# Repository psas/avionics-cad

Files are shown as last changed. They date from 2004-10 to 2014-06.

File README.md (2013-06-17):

# PSAS Schematics and Board Layouts

Main repo for all schematics and board designs on the rocket. This is
the main work of the [Avionics Team](http://psas.pdx.edu/avionics/).

To get started you'll need EAGLE CAD version 6.2 or greater.

## Directories:

 - `av3`: All files for the current rocket (2011 onwards)
 - `eagle`: CAM and script files and design rules for EAGLE CAD
 - `libraries`: Eagle libraries for differnt parts and projects
 - `lv1`: Historic boards and files for the [LV1 launch vehicle](http://psas.pdx.edu/Projects/#index2h3)
 - `lv2`: Historic boards and files for 2005 [launch of LV2.3](http://psas.pdx.edu/news/2005-08-20/)

## Naming Convention

    (rocketname)-(system-name)-[(sub-board-name)-][(sub-sub-board-name)-](version)

 - node1 = CAN Node v1, which was the PIC16F + SJA1000 design
 - node2 = CAN Node v2, which was the PIC18F + linear power supply (7805)
 - node3 = CAN Node v3, which was the PIC18F + SPS
 - node4 = USB Node v4, which is (LPC2148 ARM7 + SPSv2) 2006 capstone design
 - node5 = USB Node v5, which is (LPC2468 ARM7 + SPSv3) 2009 capstone design
 - node6 = Ethernet node v6, which is (STM32 Cortex-M4 + SPSv4) 2012 capstone design

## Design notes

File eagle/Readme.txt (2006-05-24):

PSAS EAGLE Schematics and Board Layouts

1. Naming Convention

 <rocketname>-<system-name>-[<sub-board-name>-][<sub-sub-board-name>-]<version>

 node1 = CAN Node v1, which was the PIC16F + SJA1000 design
 node2 = CAN Node v2, which was the PIC18F + linear power supply (7805)
 node3 = CAN Node v3, which was the PIC18F + SPS
 node4 = USB Node v4, which is (ARM7 + SPSv2) 2006 capstone design

2. Contents

 libraries              PSAS EAGLE Libraries (includes GPL-GPS parts)
 lv1-fc-1               LV1 flight computer (PIC17C74 + MAX197 + Presure + pyro)
 lv1-imu-1              LV1 inertial measurement unit (individual boards for each sensor)
 lv1-recovery-1         LV1 recovery/2m uplink board (PIC16F84 + DTMF decoder + Darlington pyro)
 lv1b-fc-1              LV1b flight computer (PIC17C766 + SRAM + connectors)
 lv1b-imu-1             LV1b inertial measurement unit (main board + Z axis daughter board)
 lv2-aps-1              LV2 avionics power supply
 lv2-imu-interface      LV2 inertial measurement unit node interface (uses lv1-imu-1)
 lv2-node2-connectors   LV2 node connectors
 lv2-node2-frontend     LV2 generic CAN node
 lv2-recovery           LV2 recovery/2m uplink board (PIC18F + interconnect to Tim's Rx)
 lv2-node4-frontend     LV2 generic USB node
 Readme.txt             This file
 scripts                Various useful EAGLE configurations and scripts

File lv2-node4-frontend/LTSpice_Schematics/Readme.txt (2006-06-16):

The schematic files (*.asc) only open with LTSpice/SwitcherCAD III which is available at

http://www.linear.com/company/software.jsp

When I opened up the file in PSpice for example it generated a text netlist.

There are no explicit notes about what various platforms it can run on but I used it on a Windows machine.

6/15/06

Jacob Davidson

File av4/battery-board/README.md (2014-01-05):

# AV4 Battery Board

This is a combined fuel gage, battery protection, cell balancing Smart Battery System PCB based on the BQ3060 "SBS 1.1-COMPLIANT GAS GAUGE and PROTECTION with CEDV".

# CAD and CAM

- All electronic CAD data is in the [eagle](eagle) directory.
- Design notes, Bill of Material (BOM), and functional requirements are in the [documentation](documentation) directory.
- All CAM data is in the TBD CAM directory.

# History

This board has *also* been a long time in the making. It was originally envisioned by Andrew back in 2009, started but placed on hold, and then all but finished by Bob in 2013. With the completion of the RocketNet Hub, this became the next most important project was thus picked back up by Kenny and Andrew Fall 2013. Michael finally finished it off in December 2013, and it was sent to production in Jan 2014.

# For more information

Please see <http://psas.pdx.edu/avionics>.

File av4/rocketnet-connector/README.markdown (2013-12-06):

# Rocketnet Connector

This is the standard connector we're going to use for cables between boards on
the rocket. It's built around small board-to-board connectors with a 3D printed
shroud and #2 hardware.

## Sizing Diagram

There are 3 different versions with a different number of pins

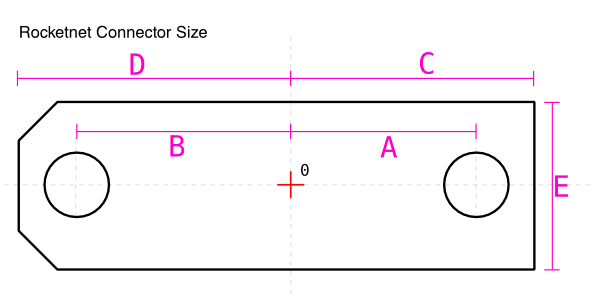
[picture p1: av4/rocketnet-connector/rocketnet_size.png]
Size diagram


**Dimentions for each version:**

 DIM |  14  |  16  |   18 
:---:| ----:| ----:| ------:
  A  |  6.9 |  7.5 |  8.135
  B  |  7.6 |  8.1 |  8.735
  C  |  8.6 |  9.1 |  9.7  
  D  |  9.2 |  9.7 | 10.3  
 C+D | 17.8 | 18.8 | 20     
  E  |  6.6 |  6.6 | 6.6

## Bolt Length

\#2 bolts: 14.5 mm

## Standoffs

Tap drill, \#50

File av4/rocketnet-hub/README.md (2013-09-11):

# Rocketnet Hub Overview

This board is the power and data distribution board for the AV3 avionics system. It has:

- Battery connector
   - Connect to the 4S1P Lithium-ion polymer battery pack
   - Also provides SMBus signals to talk with the TI BQ3060 fuel gauge IC on the battery pack.
- Umbilical connector
   - Provides shore power (usually 19V) from the umbilical cord
   - Ethernet, usually from the Launch Tower Computer (LTC)
   - Has the "rocketready" signal, a safety launch interlock.
- A TI BQ24725 battery charger IC, to charge the LiPo battery from shore power
- 7 "rocketnet" ports, which provide power and Ethernet to other rocketnet nodes (such as the Flight Computer (FC), IMU, etc).
- A Micrel KSZ8999 100Mbps Ethernet switch, which connects all of the rocketnet ports.
- An STM32F407 microcontroller that
   - Talks Ethernet to the KSZ8999 via MII
   - Switches and monitors power at each of the rocketnet ports.
   - Powers and manages the KSZ8999 Ethernet switch.

Here's a [block diagram](documentation/block_diagrams/blockdiagram.png).

# CAD and CAM

- All electronic CAD data is in the [eagle](eagle) directory
- Design notes, Bill of Material (BOM), and functional requirements are in the [documentation](documentation) directory.
- All CAM data is in the [mcu_page_combined_routed.cam](eagle/mcu_page_combined_routed.cam) directory.

# History

This board has been a long time in the making. It was originally envisioned by Andrew as replacement to the original USB LPC-based "Avionics Power System (APS)". It was then handed off to a 2012-2013 PSU ECE Capstone team, consisting of Jesse Hartley, Jackson Pugh, and Michael Woodruff. The board was checked and CAM'd by Andrew, built by [Sunstone Circuits](http://www.sunstone.com/), and then graciously assembled for free by [Screaming Circuits](http://screamingcircuits.com/). K, Theo, David, and Andrew brought the board up.

For full bring up information, including issues, fixes, modwires, and the like, see the [manufacturing and test log](documentation/mfg-and-test-log.md).

# For more information

Please see <http://psas.pdx.edu/avionics>.

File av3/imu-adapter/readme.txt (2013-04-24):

ADIS16405 IMU adapter boards

## "imu-adapter" - Adapt ADIS to node5 GFE

This board adapts the ADIS to the node5 (LPC2468 USB-based generic board). It was built, and worked.

## "imu-adapter-e407" - Adapt ADIS to Olimex STM32-E407 dev board

This board adapts the ADIS to the Olimex STM32-E407 (STM32F407 w/Ethernet) development board. It is a 1/16" single-sided PCB that must be mounted to the same mounting plane that the ADIS is mounted to. In the PCB, the holes for the ADIS and the ADIS connector are precisely spaced (see Analog Devices AN-1045 and ADIS datasheet for dimensions).

WARNING: Test points are on both sides of board, so if the board is against metal, make sure it's truly single-sided PCB.

## CAM Notes

When you run the 1 layer CAM job, you'll need to go in and edit the gerber files by hand in 'gerbv' in order to remove the ADIS mounting holes to the "right" of the actual adapter board.

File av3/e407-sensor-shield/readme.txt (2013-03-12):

This board is AV3's "sensor" sheild for an Olimex STM32-E407 development board. 

It connects the E407 board to:

- Analog Devices ADIS16405BMLZ 6DOF IMU with magnetometer (SPI)
- Invensense MPU-9150  6DOF IMU with magnetometer (I2C)
- Freescale MPL3115A2 pressure sensor (I2C)

It also brings up the Vin connection and the the ethernet jack pins in order to replace the 
coaxial jack and the ethernet jack with a RocketNet connector.

This daughter board requires the removal of the Ethernet, coaxial, and all "jumper" pin headers 
in order to fit.

TODO:

- Nothing yet!

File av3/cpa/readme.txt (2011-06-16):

Notes on v4 cylindrical patch antenna designs

2011/06/15 

Well, we've changed a few things! We've moved from the spreadsheet to a python script, and we've moved from 1.2 / 1.5 / 2.4 to 1.5 / 2.4 / 5.8 GHz. To make antennas, simply:

    run `./cpa-v4.py <frequency>`.
    Make sure there's a 'cam' directory.
    In EAGLE, open cpa-v4.cam and hit 'Process Job'.
    Use `gerbv` to sanity check the .gbx and .xln outputs.
    When you get the antennas back, see the 2004/07/03 instructions below to cut them out.

============================================================================================================================================================================

Notes on the v3 cylindrical patch antenna designs

2004/08/04

1.  Moved epsilon_r values to 2.20066 based on Tim's new calcs.

2.  Fixed 0.5Zin to 100 ohm 1/4 wave transformer on wifi antenna.

2004/08/03

1.  Added 0.010" on each side of the patch (near the seam) so we can sand off the edge to make it fit "perfectly".

2.  Moved screws that pierced the patch to the middle of the patch. Better electrically, didn't seem much worse mechanically.

3.  Removed the first 1/4wave transformer in the wifi antenna and replaced it with Zin feeds combining into a Zin/2 feed. The Zin/2 feed is then transformed to 100 ohms by a Zin/2 to 100 ohm 1/2 wave transformer, at which point it makes a 50 ohm line as usual.

4.  Added more space to the top and bottom of the PCB antenna so that the screw heads are at least 5h away from any radiator/microstrip.

5. Moved from the simplistic book-based patch length formula (with the 0.49 kludge factor) to the more elegant derived length model.

2004/07/30

1.  Cutting out the antennas:
    a. The patches should be cut out with the exacto blade splitting the 0.01" trace on the top and bottom of the board. This will require removing the 0.005" traces on either side, but there's not much to do about that (possible solution: we get the boards silk screened).
    b. The wide traces on the left and right are cut-out alignment traces; the excacto blade should go on the outside of the radiating patch and the inside of the alignment traces - thus when the board is cut out properly, the alignment traces won't be on the board.

2.  There are three elements stacked on top of each other at each screw location:
    a. The widest circle (located on on the tplace layer) is the outline of the counter-sunk #4 screw head.
    b. The middle circle (located on on the bplace layer) is the outline of the #4 screw hole drilled in the airframe.
    c. The smallest cicle, with the hour-glass symbol in it, is a 0.05" alignment hole drilled in the antenna PCB.
    
3.  The large circle located at the feedpoint (located on the bplace layer) is the outline of the 0.5" hole cut into the airframe in order to feed through the patch's SMA connector.

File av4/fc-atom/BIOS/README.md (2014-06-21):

The Atom board has an SPI EEPROM socket which holds 2MB of fun.  Everything the Atom needs for initial bootup lives here.  BIOS, its settings, and any other magic Intel goodness included.  We really just want the settings, but a different BIOS version would be confused by our settings binary segment.  So we may as well just grab the whole 2MB.  With a really slow interface like the BusPirate, this will cost you less than 10 minutes.

Kenny says to ask him questions about this process, if you have any.  There are all sorts of ways to drive SPI.  Here we use flashrom, which is probably packaged and available in your favorite Linux distro.  It supports many physical interface devices including the BusPirate.

Useful stuff:
+ http://flashrom.org/Bus_Pirate
+ https://www.sparkfun.com/products/9544
+ http://www.digikey.com/product-detail/en/5250/501-1311-ND/745102

An example run looks something like this:

```
$ time flashrom -p buspirate_spi:dev=/dev/ttyUSB0 -r SST25VF016B_dist.bin
flashrom v0.9.6.1-r1563 on Linux 3.11.0-20-generic (x86_64)
flashrom is free software, get the source code at http://www.flashrom.org

Calibrating delay loop... OK.
Found SST flash chip "SST25VF016B" (2048 kB, SPI) on buspirate_spi.
Reading flash... done.

real    8m9.453s
user    0m7.022s
sys     0m30.182s
```

If you want a dump of the active EEPROM contents directly from the Flight Computer, it could look like this:

```
root@psas:~# time flashrom -p internal -c SST25VF016B -r SST25VF016B_test.bin
flashrom v0.9.7-r1782 on Linux 3.14-1-amd64 (x86_64)
flashrom is free software, get the source code at http://www.flashrom.org

Calibrating delay loop... OK.
Found chipset "Intel ICH8M". Enabling flash write... OK.
Found SST flash chip "SST25VF016B" (2048 kB, SPI) at physical address 0xffe00000.
Reading flash... done.

real    0m2.268s
user    0m2.252s
sys     0m0.008s
```

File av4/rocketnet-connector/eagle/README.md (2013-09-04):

These files are PCBs for the rocketnet connector series. There are three different sizes:

14 pins = battery pack connector
16 pins = rocketnet connector
18 pins = umbilical connector

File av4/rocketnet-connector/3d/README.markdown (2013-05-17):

# Rocketnet But CAD Assembly

Files:

 - `rocketnet-connector-12pin.assemb.fcstd`: 12 pin version, full assembly
 - `rocketnet-connector-14pin.assemb.fcstd`: 14 pin version
 - `rocketnet-connector-16pin.assemb.fcstd`: 16 pin version

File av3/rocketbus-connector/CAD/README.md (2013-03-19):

# CAD Models for RocketBus Connector

Bare connectors tend to fall off rockets, so we have 3D printed plastic parts to accept bolts and lock down our cables.

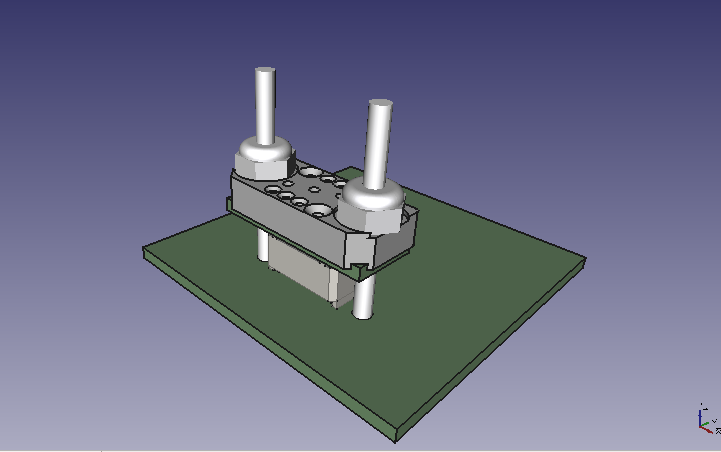
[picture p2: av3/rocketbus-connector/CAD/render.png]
Connector Render


## FreeCAD

Documents are made in [FreeCAD](http://free-cad.sourceforge.net/).

Files with `.part.` in the name are drawings of just a particular solid part.

`rockebus.assem.fcstd` is the full assembly with conncetors, bolts and boards all modeled. Printable parts can be exported by highlighting them and choosing File > export.

Version 0.2 printed at the [Electronics Prototyping Lab](http://psu-epl.github.com/) at PSU.

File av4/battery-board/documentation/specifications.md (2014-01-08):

# AV4 Battery Board Design Notes

## Overall Power System Design

At peak use, our avionics system is designed to handle about a (,30,50) W load. Our current best guess:

- FC = 15W
- RNH = 2W
- WiFi = 5W
- GPS = 1W
- IMU = 1W
- RC = 10W
- DV = 5W
- **Total** = 39 W

In terms of current, that's 2-3 A @ 16.7V or 3-5A @ 10V. That gives us a discharge current rating of (,3,5) A.

## Specifications

- MUST 
   - Measure pack voltage which can be (9,16.7,20) V.
   - Monitor pack current of (0.001,,5) A. 
   - Monitor charge ("coulomb counter") which can be (0, 4, 8) AHr with an accuracy of (,5,10)%.
   - Monitor battery pack temperature (-10,25,+80) deg C.
   - Be rated for (1,1.5,) C continuous charge and discharge currents (which would be (4,6,) A for an 4 AHr pack).
   - Provide electronic short circuit protection of 1.5 C (6 A for an 4 AHr pack), while not false-triggering on turn on capacitive transients of 100 uF.
   - Provide fused short circuit protection of (,2,5) C (which would be (,8,20) A for an 4 AHr pack), while not false-triggering on capacitive transients of 100 uF.
   - Fit on front of battery pack (,67 x 24,) mm.
   - Be shielded such that metal tools contact will not cause a short circuit in the battery.
   - Not have any components or leads that protrude into the battery compartment (excluding thermistors).
- SHOULD
   - Monitor the voltage on each cell.
   - Do cell balancing.
   - Handle deeply discharged batteries.
   - According to [[RocketNames]], the battery board components are all numbered in the 1xx regime.

## Tiered Overcurrent Protection

We have multiple tiers of overcurrent protection. In order of severity, we have:

- Local node OCP.
- TPS2450 circuit breaker chips on the RNH, custom set to a specific node at (0.5,,4) A.
- Battery board continuous overcurrent protection from the BQ3060 at 1.5C (,6,)A.
- 10 A fuse on the battery board; must handle 10-20A spikes but should blow if continuous.
- 20 A fuse on the battery breakout boards in each battery cell.

## Board layout notes

- Running board on OSH Park 4 layer process (5/5 design rules).
- We don't really need the 4 layers, but by doubling up on all four layers, we make 1 + 0.5 + 0.5 + 1 = 3 oz copper weight, which is perfect for high power.
- We're not pushing the design rules.

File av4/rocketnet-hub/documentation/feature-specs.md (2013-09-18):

# Features and Behaviors of the RocketNet Hub

TODO: This is just a rough draft.

## Modes

0. Boot mode
   - Check out saved state (armed/active).
1. Sleep mode (idle)
   - KSZ completely off.
   - All nodes are off.
   - Set interrupt on external GPIO (ACOK rising edge).
   - Go into deep sleep (all clocks off).
   - Goal: absolute minimum power consumpt (&lt; 5 mA)
   - Charge battery if shore power on (requires wakeup every 175 s to ping the BQ)
2. Debug mode (utility mode)
   - Ignores shore power on/off, otherwise just like active mode
   - Can not transition from debug to armed.
2. Active mode (startup/running mode)
   - KSZ is on.
   - One or more nodes are on.
   - Awake and looking for packets, acting on packets.
   - Monitoring battery voltage.
   - Charging battery when possible.
   - Can load power configurations (see below)
3. Armed mode (in flight)
   - Write armed state to file + last power configuration in case of restart
   - Everything on that should be on
      - Default configuration
      - Power configurations mapped to flight status?
   - Actively turning things back on that over current some number of times.
   - Resetting the KSZ and if no packets are getting through.
   - Resetting nodes (including the FC) if watchdog packets don't come through.
   - Broadcasting information on node power switches, current, voltage, etc.

## Mode Transitions

- Boot -> Armed
   - State saved file
- Boot -> Active
   - Shore power on
- Boot -> Sleep
   - Shore power off

- Sleep -> Active: 
   - Shorepower on (ACOK rising edge)

- Active -> Sleep:
   - Shore power: off
   - Nodes: all off || Vsys &lt; 12 V
   - Sleep command received

- Active -> Armed:
   - Arm command received (written to flash)

- Armed -> Active:
   - Disarm command received

- Active <-> Debug:
   - On debug start/stop command

- Debug -> Sleep:
   - Go to sleep
   
### Notes

- Send a "you're going to get shut down" packet some time before shutting off a node

## Command packets

- Turn on/off the KSZ
- Turn on/off any node
- Go to sleep
- Arm
- Disarm
- Transmit data packets
- Node-sepcific watchdog packets (each node sends it a ping, else the RNH power cycles it)

## Data packets

- Time
- Mode
- Shore Power Information
  - Shore power on/off
  - Shore power current (via IOUT)
- Battery charging info
  - Charging on/off
  - Battery charge current (via IOUT)
  - System voltage (shore power voltage when shore power on, battery voltage when shore power off)
- Power switches
   - KSZ power state
   - Node switch state, current from each node
- Future: BQ3060 battery state
   - Precise battery voltage, current, SOC, charge/discharge status, etc.
- Watchdog
   - Number of watchdog reboots
   - Time since last packet from each node

## Notes

- What's the current draw in each mode? How many hours can we last in each?
- We should send "arm" as a broadcast packet, and everyone could record the timestamp to sync their clocks.
- GPS could broadcast precise clock packets?
- Pre-broadcast-time packet could clear bus, then send time packet, to get real-time behavior.

## Quiescent current / "Shelf life"

Since:

- BQ24725 draws 20 uA when running directly from the battery without charging.
- The LTM8023 draws a couple of hundred microamps with no load.
- The STM32 in sleep mode draws hundreds of microamps.
- We have some current bleed through the link LEDs since they're running off the 3.3V supply (and why are they?).

Based on this, we should expect the quiescent draw of the whole RNH board of probably ~ 5 mA. Measured on bring up was ~ 3 mA. At 3 mA, that's about 1.5 months of life on a **fully charged** battery pack. On a fully depleted pack, this could kill the pack in a day or two. For this reason, we need to disconnect the battery when shore power is off and the avionics system is just sitting on the shelf.

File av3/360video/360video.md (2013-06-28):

Using H11F1 opto-isolator FET chip between APS "RC" output and GoPros "start" line. The FET grounds out the "start" line, and they all turn on and start recording.

We tested this system on the Agilent power supplies, and a forward curent I_f = 1 mA turned them on no problem.

The APS will run the H11F1 at 3.3V, Vf = 1.2 V so R = 2.1V/3mA = 700 ohms, so call it 750 ohms = 2.8 mA ish.

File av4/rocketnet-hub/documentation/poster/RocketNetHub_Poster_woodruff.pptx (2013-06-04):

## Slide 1

PSAS RocketNet Hub | Capstone 2012-2013

PSAS: Andrew Greenberg | Capstone Team : JJ Hartley, Jackson Pugh, and Michael Woodruff | Faculty Advisor: Dr. Richard Campbell

Overview
The capstone sponsor, Portland State Aerospace Society (PSAS), designs, builds, and launches high-power rockets. Their 2012-2013 Capstone project is a power management and communications solution for use in both their current and next generation launch vehicles. To accommodate the size and weight restrictions imposed by the physical characteristics of the current launch vehicle, the decision was made to pursue a highly integrated solution which would provide for all the power

Subsystem Design
Communications:
Initially specified as USB, the communications subsystem was changed to operate using the CAN Bus due to latency. This was then re-specified again to use 100Mbps Ethernet. A 10/100 Mbps 8+1 port switch-on-chip from Micrel was selected as it was the only device with the required functionality available to small-scale designers.
Microcontroller:
PSAS recently switched to STM32 microcontrollers for their nodes and requested that the same MCU be used to control this board. It is a compact ARM Cortex based microcontroller that is well suited to scalable embedded designs. The MCU’s primary functions are to control the battery charger, Ethernet switch, and each node’s power switch. Secondary functions are monitoring the battery’s charge state, current consumption of each node, and to reset the Ethernet switch if it enters a fault condition.
Power Domains:
The complexity of the this project was greatly increased by the requirement to accommodate five separate power domains on the board. There are two primary supplies, an 18VDC external supply and a four-cell battery pack. These feed the high voltage domain that powers the seven nodes and a 3.3V switching power supply. The 3.3V power domain supplies the onboard logic and a 2.1V LDO. The 2.1V power domain is used by the Ethernet switch.
Power Distribution:
Each of the seven nodes can be switched on or off by the MCU. By using a hot swap controller with integrated power FET, this solution allows for current ramping when a node is turned on, fault handling, and current monitoring all from a single 4mm x 4mm IC.
Battery charger:
The rocket’s battery is charged using an external 18VDC supply. This subsystem is built around a lithium polymer charger IC that monitors the battery during charging to prevent overheating and allows the current draw to be monitored while discharging.

Department of Electrical and Computer Engineering

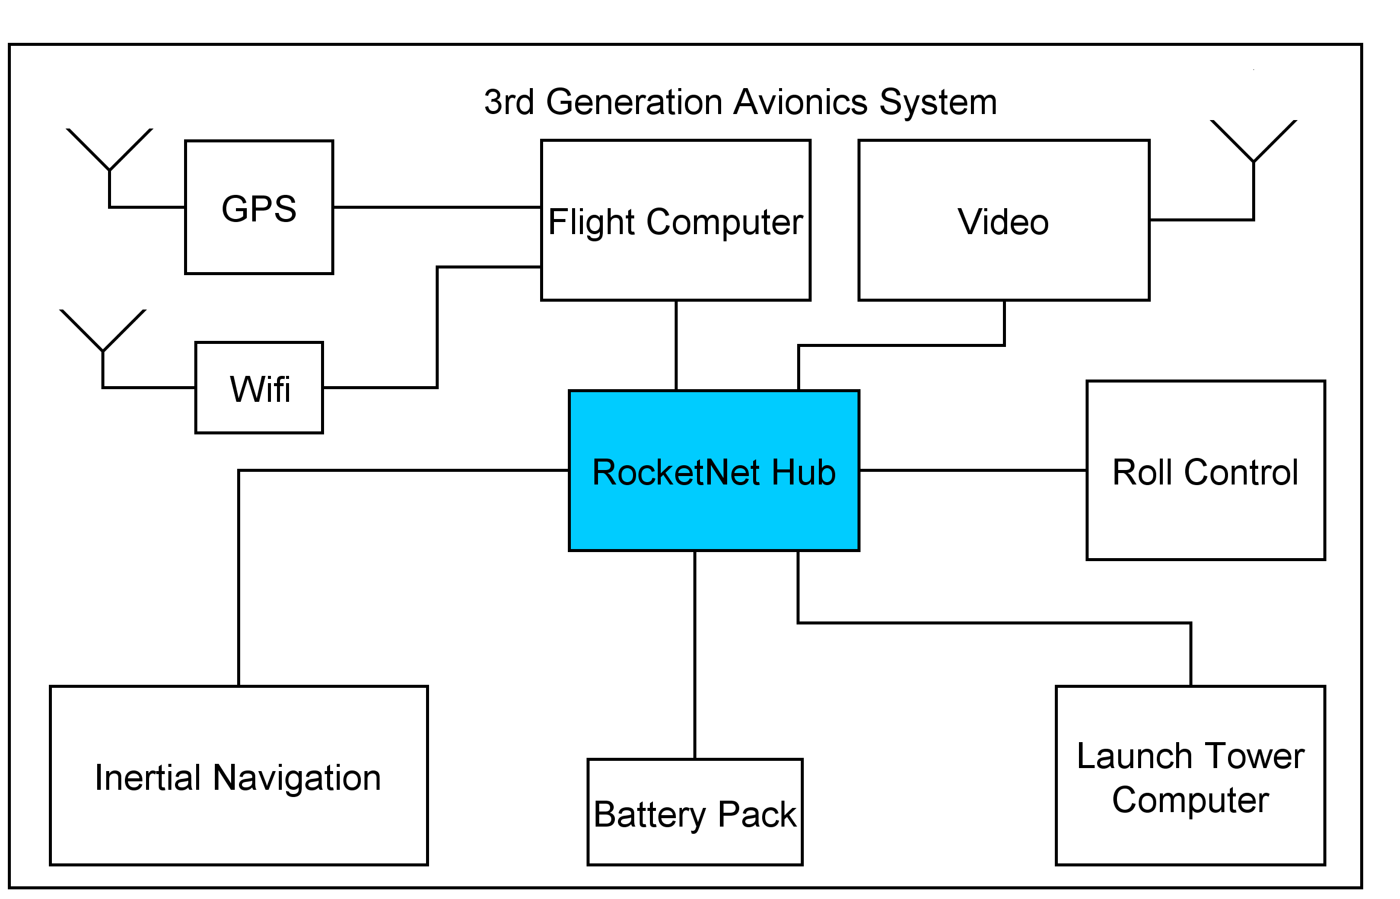
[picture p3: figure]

management functions as well as provide low
latency communication between all of the electronic
systems used in-flight on a single 6-layer PCB
with components placed on both sides.

Requirements
- Support seven nodes
- High reliability and fail-safe design
- Provide low latency inter-node communications
- Independent power management for each node in-flight and battery management pre-flight
- High efficiency switching power regulation from high voltage battery pack for low voltage logic
- Low-power consumption when in standby mode
- Charge the four-cell battery in under two hours

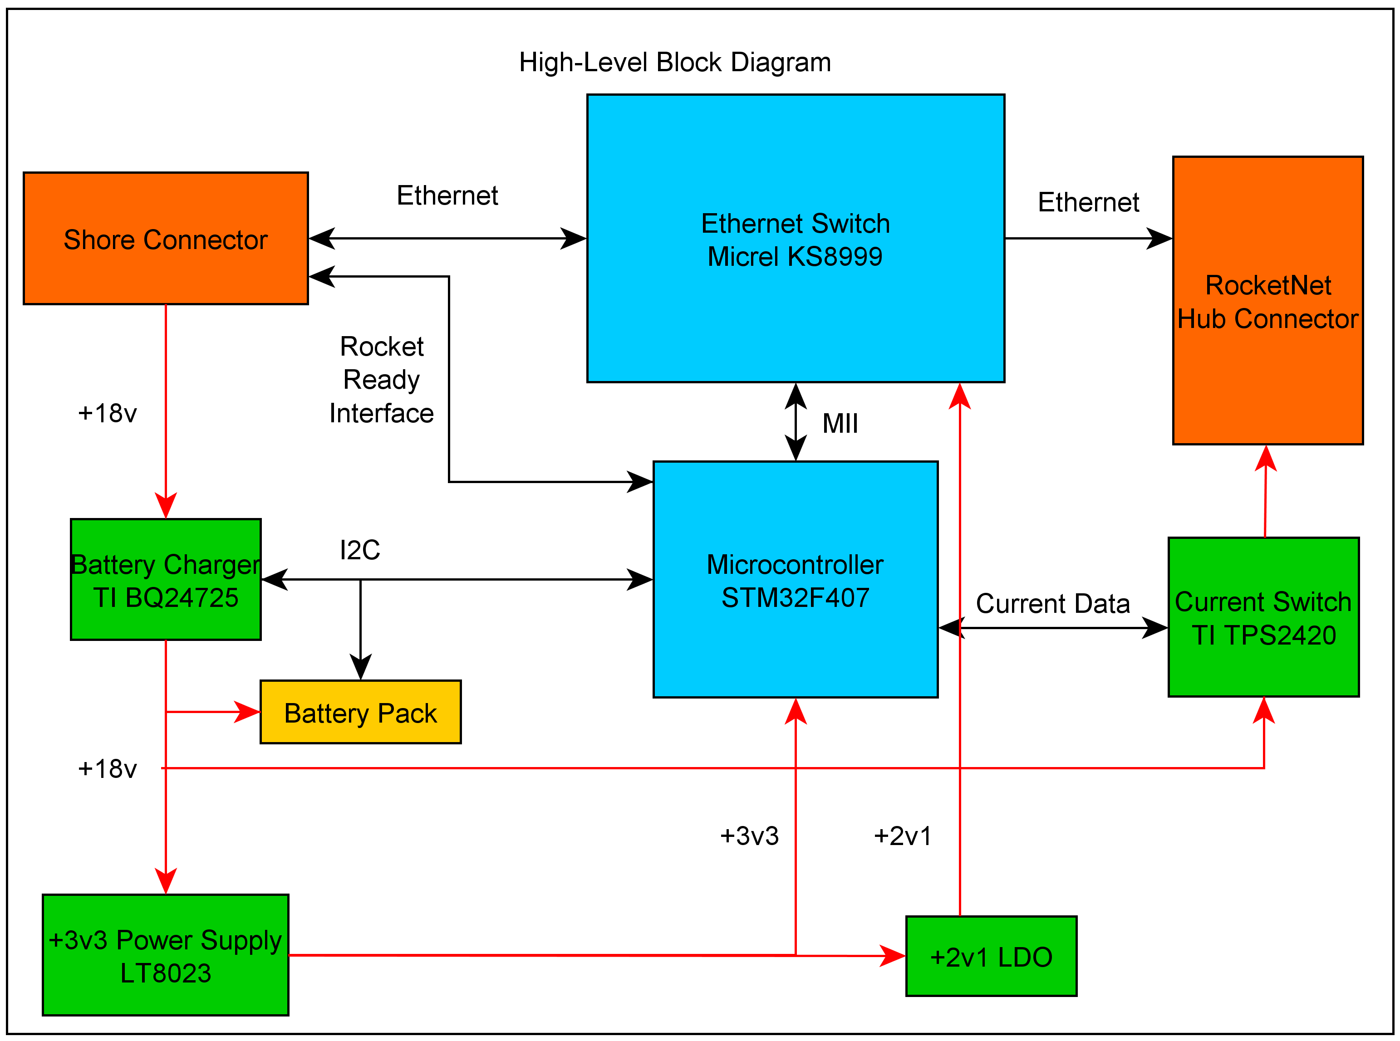
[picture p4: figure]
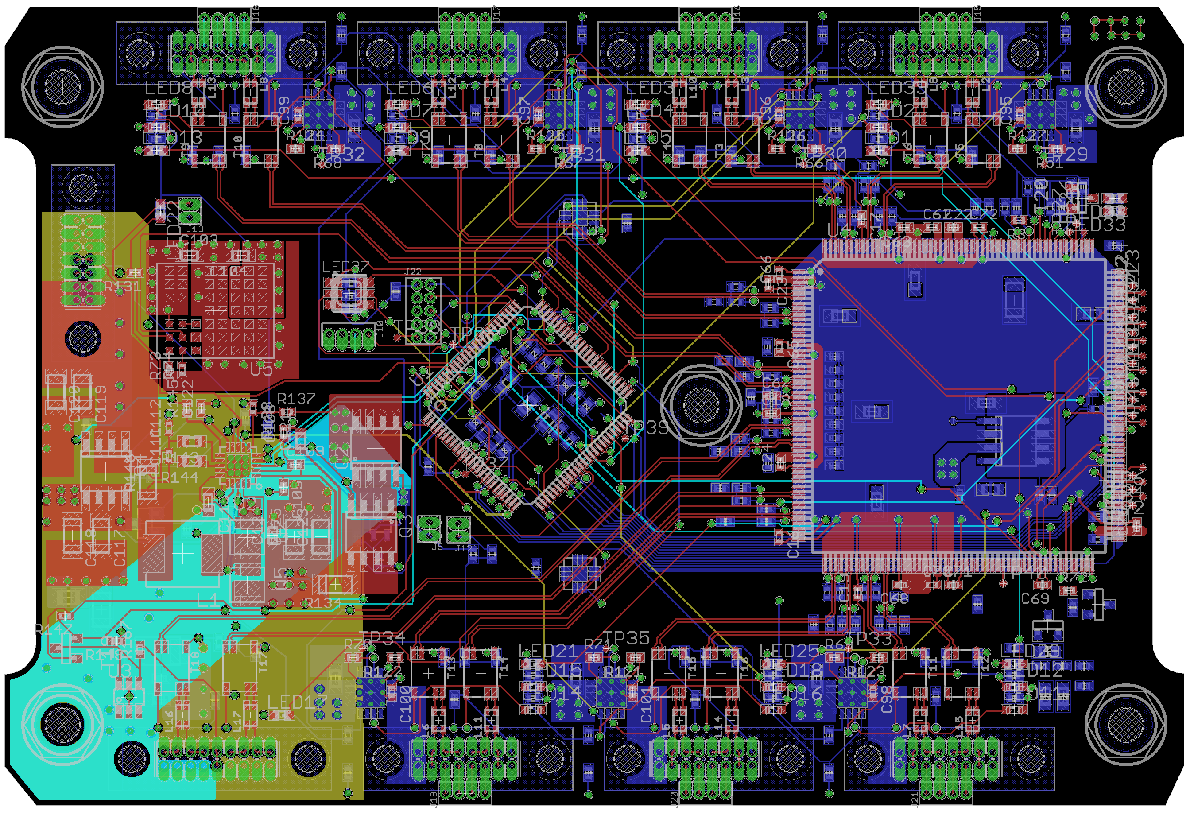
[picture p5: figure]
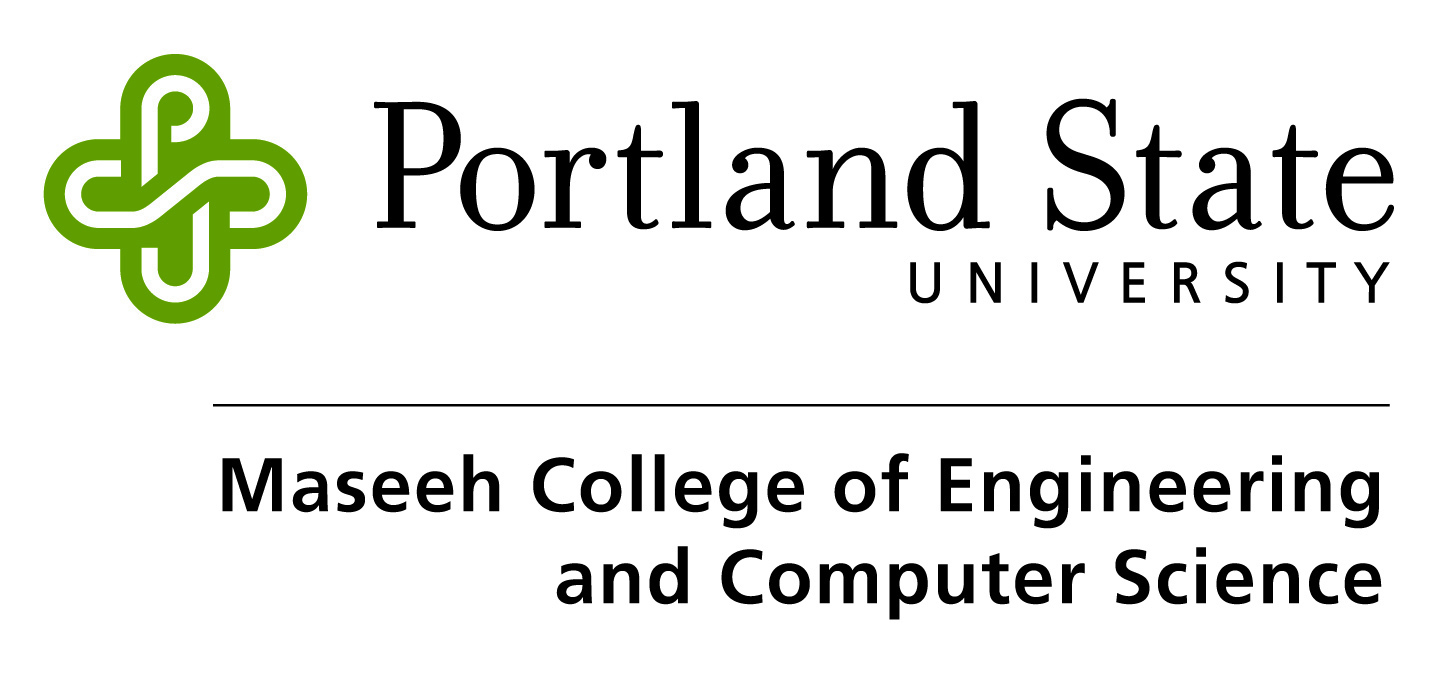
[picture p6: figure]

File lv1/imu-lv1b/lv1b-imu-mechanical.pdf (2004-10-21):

## LV1b imu-analog

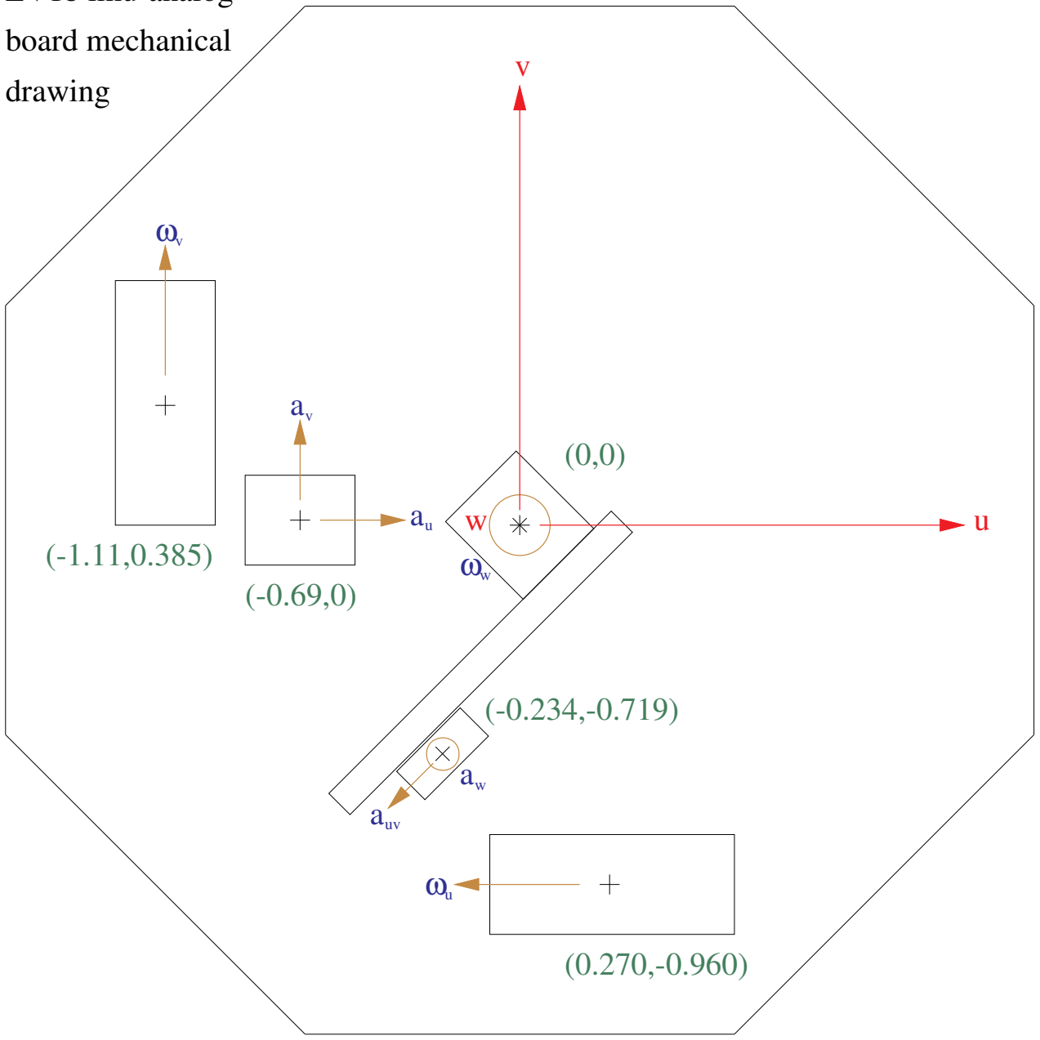
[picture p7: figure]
auv; board mechanical; drawing

accelerometer arrows indicate the sensitive axis in the direction of positive output

circles indicate the sensitive axis is up out of the plane of the drawing

gyro arrows indicate the sensitive axis, positive output follows the right hand rule

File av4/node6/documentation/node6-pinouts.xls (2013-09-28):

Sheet: Pins
Used: |  | 48
Free: |  | 52
PIN |  | FUNC1 | FUNC2 | FUNC3 | FUNC4 | FUNC5 | Notes
PA | 0 | UART4_TX | TIMER | WAKEUP
PA | 1 | ETH_RMII_REF_CLK | UART4_RX | TIMER |  |  | Ethernet PHY
PA | 2 | ETH_MDIO | USART2_TX | TIMER |  |  | Ethernet PHY
PA | 3 | USART2_RX | TIMER
PA | 4 | SPI1_NSS | SPI3_NSS
PA | 5 | SPI1_SCK | TIMER
PA | 6 | SPI1_MISO | TIMER
PA | 7 | ETH_RMII_CRS_DV | ETH_MII_RX_DV | SPI1_MOSI/ | TIMER |  | Ethernet PHY
PA | 8 | MCO1 | I2C3_SCL | TIMER |  |  | Ethernet PHY
PA | 9 | OTG_FS_VBUS | USART1_TX | I2C3_SMBA | TIMER |  | Debug connector
PA | 10 | OTG_FS_ID | USART1_RX/ | TIMER
PA | 11 | OTG_FS_DM | CAN1_RX | TIMER |  |  | Debug connector
PA | 12 | OTG_FS_DP | CAN1_TX | TIMER |  |  | Debug connector
PA | 13 | JTMS-SWDIO |  |  |  |  | JTAG connector
PA | 14 | TCK-SWCLK |  |  |  |  | JTAG connector
PA | 15 | JTDI | SPI3_NSS | SPI3_NSS | TIMER |  | JTAG connector
PB | 0 | TIMER
PB | 1 | TIMER
PB | 2 | BOOT1 |  |  |  |  | Tie low during startup and wakeup
PB | 3 | JTDO | SPI3_SCK | SPI1_SCK | TIMER |  | JTAG connector
PB | 4 | NJTRST | SPI3_MISO | SPI1_MISO | TIMER
PB | 5 | I2C1_SMBA | CAN2_RX | ETH_PPS_OUT | SPI1_MOSI | SPI3_MOSI
PB | 6 | I2C1_SCL | CAN2_TX | USART1_TX/ | TIMER |  | Debug connector
PB | 7 | I2C1_SDA | USART1_RX |  |  |  | Debug connector
PB | 8 | SPI2_NSS | I2C1_SDA | CAN1_TX
PB | 9 | SPI2_NSS | I2C1_SDA | CAN1_TX
PB | 10 | SPI2_SCK | USART3_TX
PB | 11 | ETH_RMII_TX_EN | I2C2_SDA | USART3_RX | TIMER |  | Ethernet PHY
PB | 12 | ETH_RMII_TXD0 | SPI2_NSS | I2C2_SMBA | CAN2_RX |  | Ethernet PHY
PB | 13 | ETH_RMII_TXD1 | SPI2_SCK | CAN2_TX | TIMER |  | Ethernet PHY
PB | 14 | SPI2_MISO | TIMER
PB | 15 | SPI2_MOSI | TIMER
PC | 0 | -
PC | 1 | ETH_MDC |  |  |  |  | Ethernet PHY
PC | 2 | SPI2_MISO
PC | 3 | SPI2_MOSI
PC | 4 | ETH_RMII_RX_D0 |  |  |  |  | Ethernet PHY
PC | 5 | ETH_RMII_RX_D1 |  |  |  |  | Ethernet PHY
PC | 6 | USART6_TX | TIMER
PC | 7 | USART6_RX | TIMER
PC | 8 | SDIO_D0 | TIMER |  |  |  | MicroSD card
PC | 9 | SDIO_D1 | MCO2 | I2C3_SDA | TIMER |  | MicroSD card
PC | 10 | SDIO_D2 | SPI3_SCK | USART3_TX |  |  | MicroSD card
PC | 11 | SDIO_D3 | UART4_RX | SPI3_MISO | USART3_RX |  | MicroSD card
PC | 12 | SDIO_CK | UART5_TX | SPI3_MOSI |  |  | MicroSD card
PC | 13 | - |  |  |  |  | NOTE: Kept energized when on Vbat
PC | 14 | OSC32_IN |  |  |  |  | RTC 32KHz xtal
PC | 15 | OSC32_OUT |  |  |  |  | RTC 32KHz xtal
PD | 0 | CAN1_RX
PD | 1 | CAN1_TX
PD | 2 | SDIO_CMD | UART5_RX | TIMER |  |  | MicroSD card
PD | 3 | -
PD | 4 | -
PD | 5 | USART2_TX
PD | 6 | USART2_RX
PD | 7 | -
PD | 8 | USART3_TX
PD | 9 | USART3_RX
PD | 10 | -
PD | 11 | -
PD | 12 | TIMER
PD | 13 | TIMER
PD | 14 | TIMER
PD | 15 | TIMER
PE | 0 | TIMER
PE | 1 | -
PE | 2 | -
PE | 3 | -
PE | 4 | -
PE | 5 | TIMER
PE | 6 | TIMER
PE | 7 | TIMER
PE | 8 | TIMER
PE | 9 | TIMER
PE | 10 | TIMER
PE | 11 | TIMER
PE | 12 | TIMER
PE | 13 | TIMER
PE | 14 | TIMER
PE | 15 | TIMER
PH | 0 | OSC_IN |  |  |  |  | 25 MHz xtal
PH | 1 | OSC_OUT |  |  |  |  | 25 MHz xtal
BOOT0 |  | BOOT0 |  |  |  |  | Debug connector, but pull down on board.
NRST |  | !RESET |  |  |  |  | Debug connector
VBAT |  | PWR |  |  |  |  | To RTC backup supply: supercap or coin cell
PWR | 0 | PWR
PWR | 1 | PWR
PWR | 2 | PWR
PWR | 3 | PWR
PWR | 4 | PWR
PWR | 5 | PWR
PWR | 6 | PWR
PWR | 7 | PWR
PWR | 8 | PWR
PWR | 9 | PWR
PWR | 10 | PWR
PWR | 11 | PWR
PWR | 12 | PWR
PWR | 13 | PWR
PWR | 14 | PWR
PWR | 15 | PWR

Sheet: JTAG Connector
JTAG Connector

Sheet: Debug Connector
Pin | STM32 PIN |  | FUNC1 | Notes
1 | PA | 9 | OTG_FS_VBUS | USB /dev/ttyACM0
2 | PA | 11 | OTG_FS_DM | USB /dev/ttyACM0
3 | PA | 12 | OTG_FS_DP | USB /dev/ttyACM0
4 | PB | 6 | USART1_TX/ | Debug UART
5 | PB | 7 | USART1_RX | Debug UART
6 | BOOT0 |  | BOOT0 | Use UART bootloader
7 | NRST |  | !RESET | Reset
8 | Vcc |  | Vcc | 3.3V ("Vtarget")
9 | GND |  | GND | GND
10 | ? |  | ? | Misc - Either to breakout pin or GPIO

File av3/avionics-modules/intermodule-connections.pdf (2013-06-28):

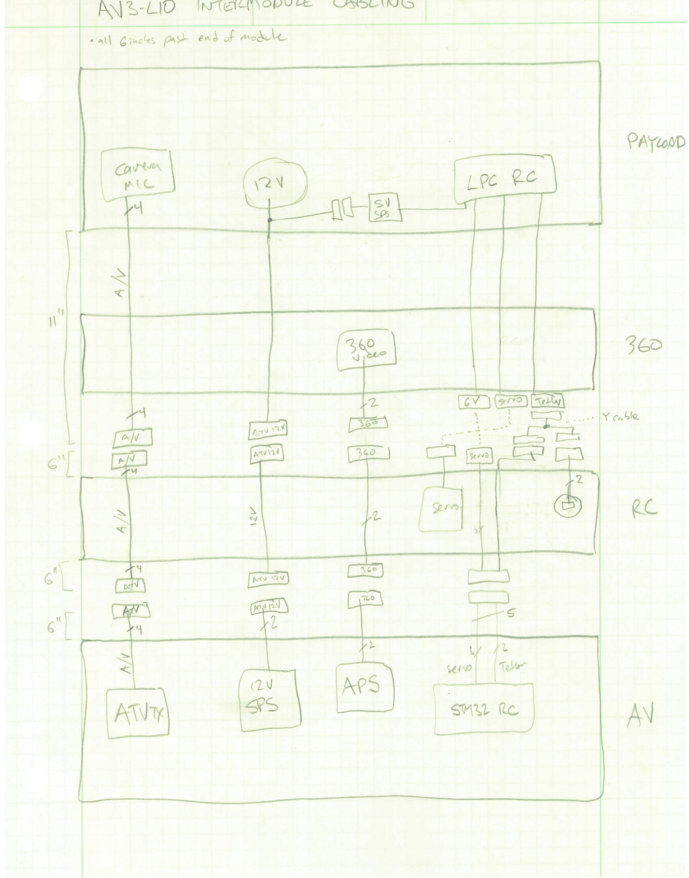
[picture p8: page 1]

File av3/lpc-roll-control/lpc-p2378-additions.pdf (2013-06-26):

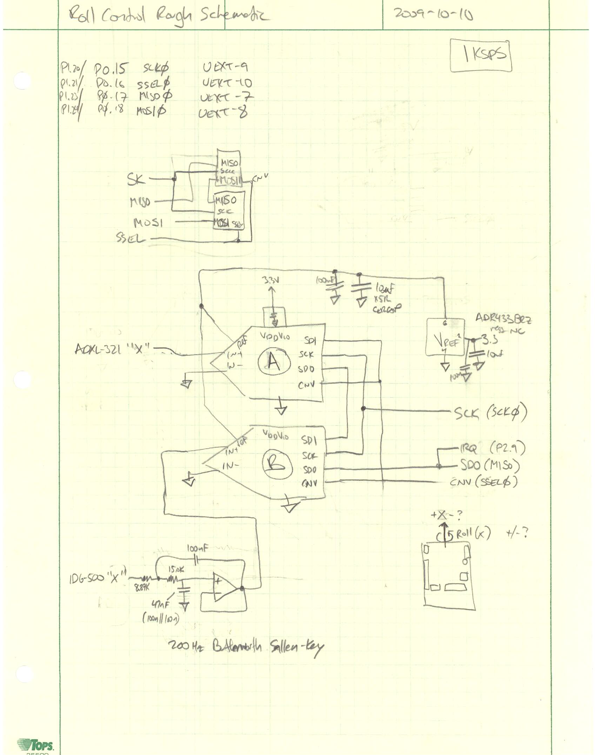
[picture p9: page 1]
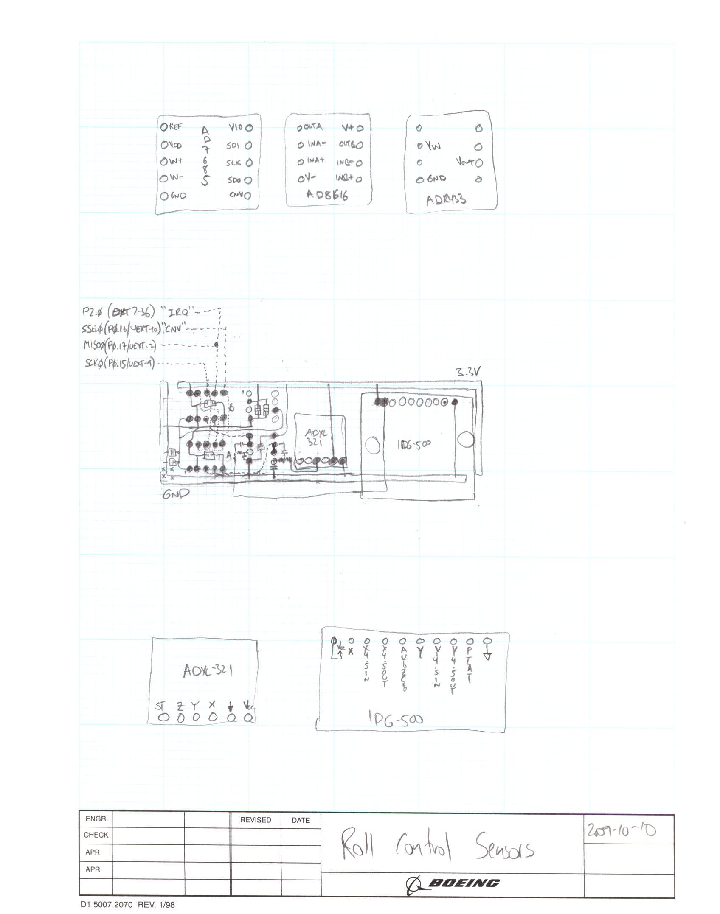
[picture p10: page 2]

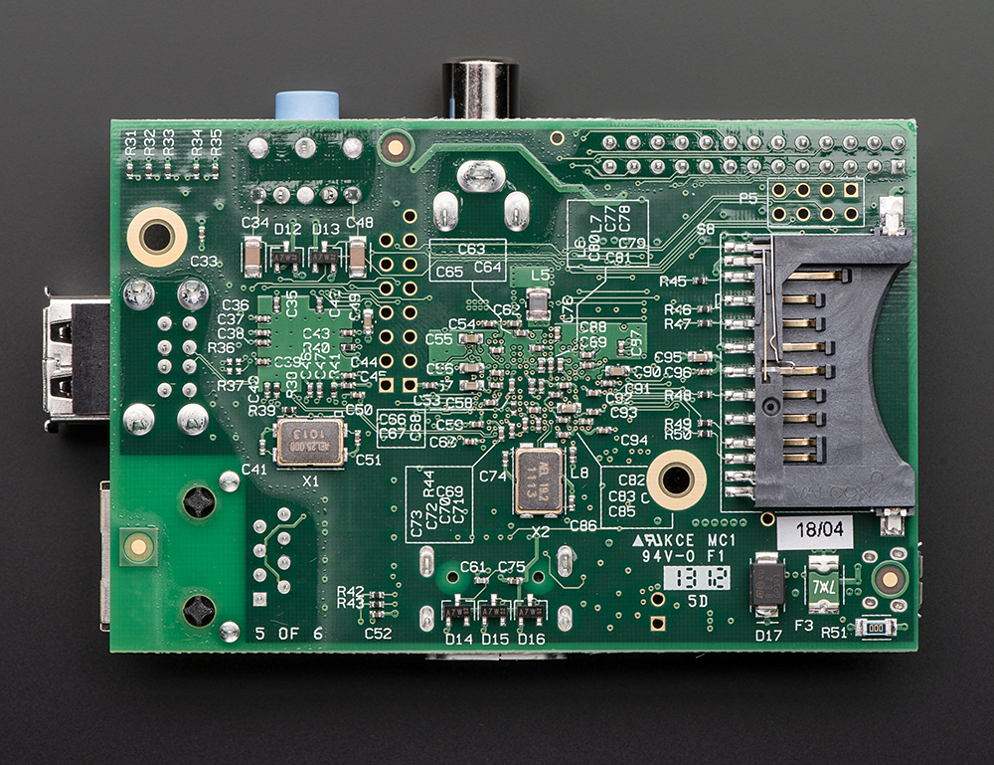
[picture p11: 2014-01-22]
av4/raspi-camera/datasheets/modelb_bottom.jpg

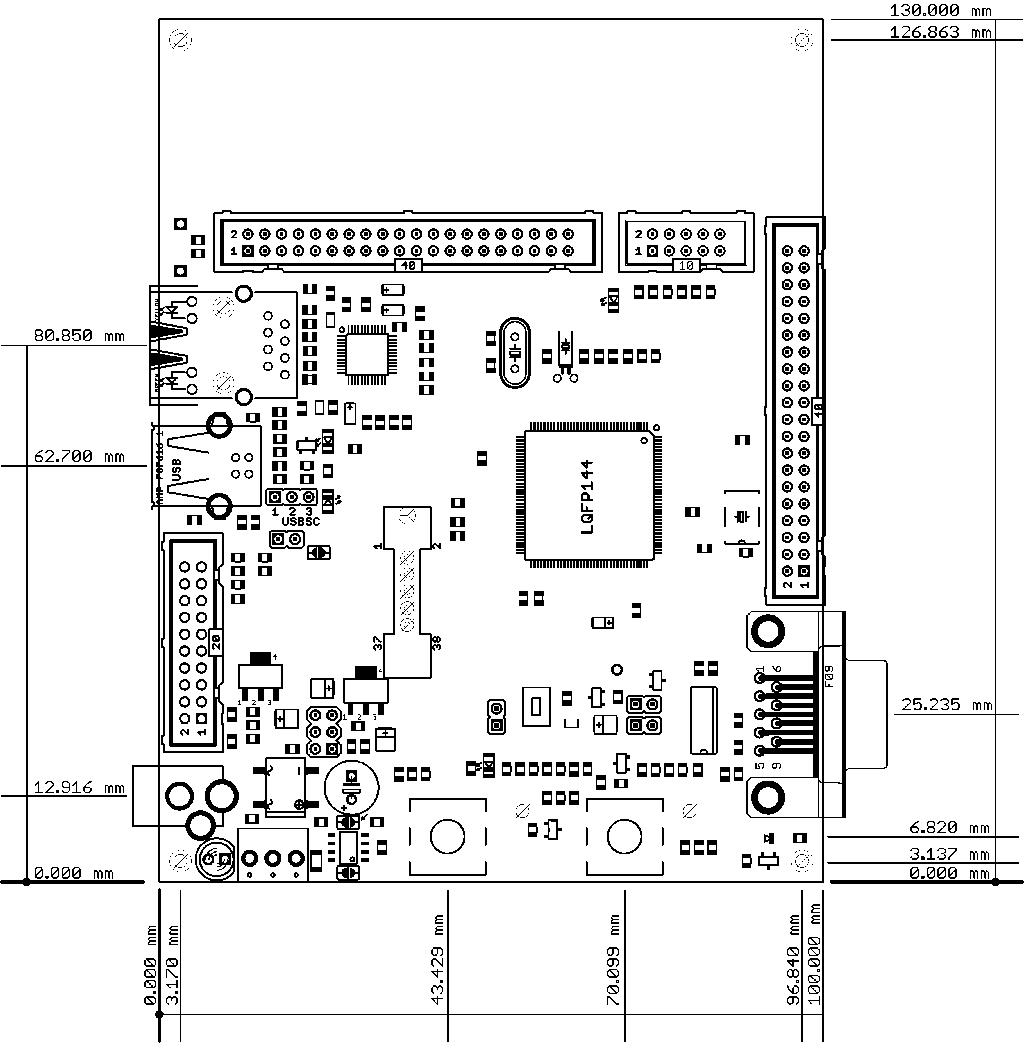
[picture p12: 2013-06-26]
av3/lpc-roll-control/LPC-P2378_Rev-B-dimensions.gif

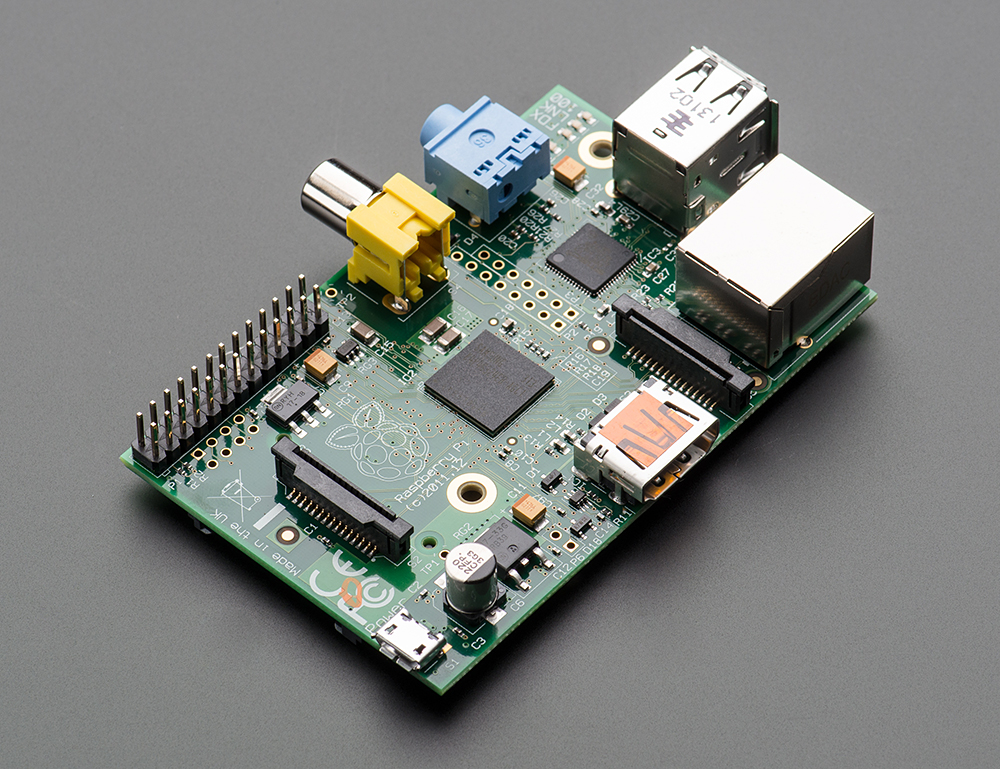
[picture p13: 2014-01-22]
av4/raspi-camera/datasheets/modelb_orthagonal.jpg

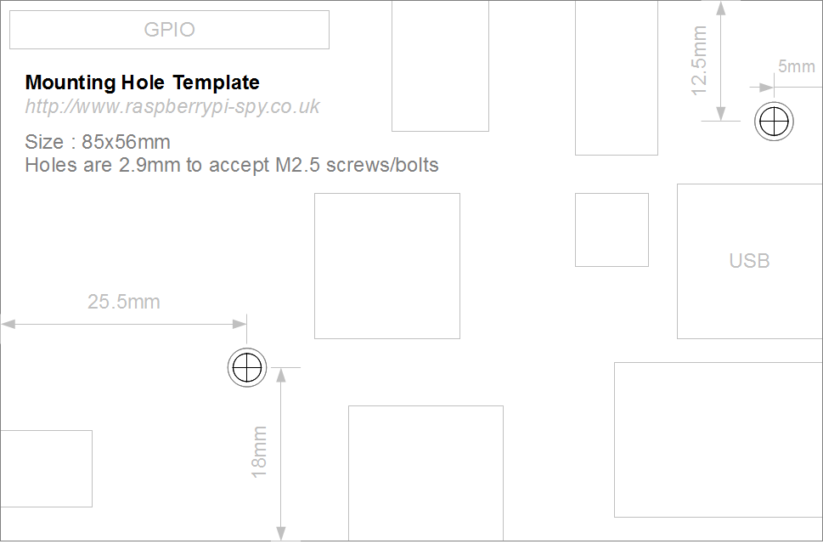
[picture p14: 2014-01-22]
av4/raspi-camera/datasheets/Raspberry-Pi-Mounting-Hole-Template.png

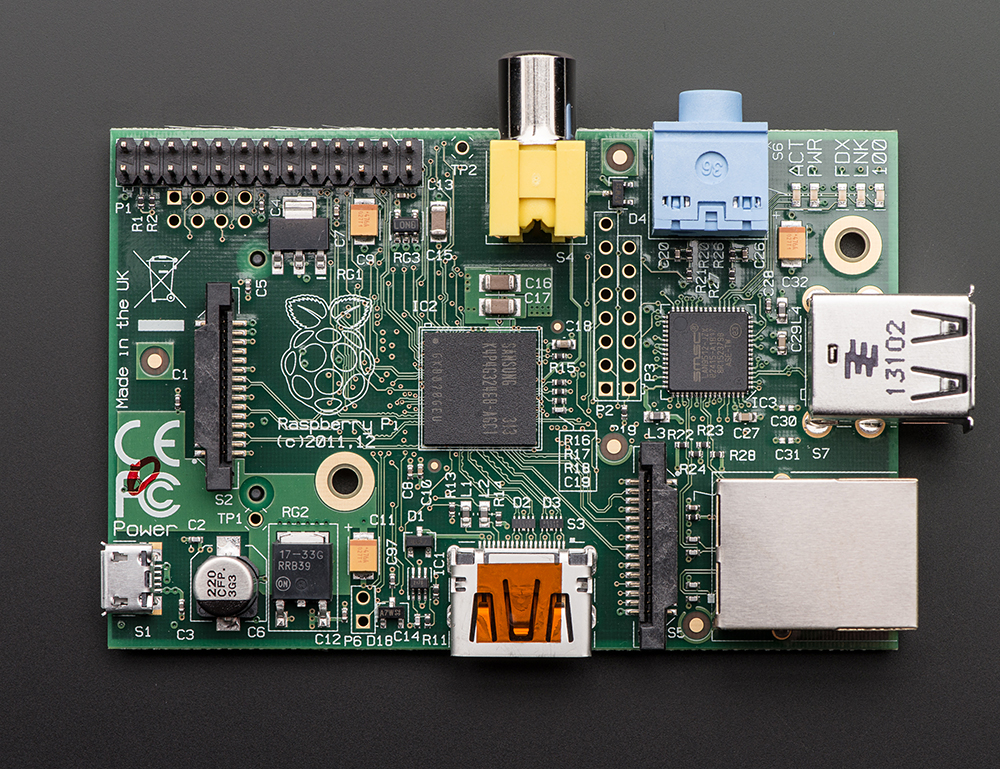
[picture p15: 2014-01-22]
av4/raspi-camera/datasheets/modelb_top.jpg

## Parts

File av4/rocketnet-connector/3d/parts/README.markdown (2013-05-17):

# Parts For CAD Assembly

**Manafacturer Parts**

STEP files from the manafacturer

 - `m50-3150642_asm.stp`: 12 Pin Female Connector
 - `m50-3150742_asm.stp`: 14 Pin Female Connector
 - `m50-3150842_asm.stp`: 16 Pin Female Connector
 - `m50-3500642_asm.stp`: 12 Pin Male Connector
 - `m50-3500742_asm.stp`: 14 Pin Male Connector
 - `m50-3500842_asm.stp`: 16 Pin Male Connector

**PSAS Parts**

Sub assembly

 - `Base_CircuitBoard.stp`: Plane circuit board base.
 - `Daughter_Board.part.fcstd`: FreeCad document of daughter board
 - `Daughter_Board.stp`: Step file export of daughter board
 - `no2_hex_screw.part.fcstd`: #2 Hex head screw freecad doc
 - `no2_hex_screw.stp`: #2 hex head screw part

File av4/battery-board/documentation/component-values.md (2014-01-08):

## Component Value Calculations

### F100 main fuse - 10A fast blow 1206 - LittleFuse 0501010.WR (DK F2919CT-ND)

**Purpose:** F100 is the main fuse that provides emergency overcurrent, over voltage (via D100), and reverse voltage (via D100) protection.

**Notes:** It's a 10A fuse in a 1206 package. 0.5679 Ohm resistance rated for 32V. F100 should take 10A forever, 30A @ 10s, 35A @ 1s, 42A @ 100ms, 52A @ 10ms, and and about 100A @ 1ms. During normal conditions, we expect to not pull more than 5A out of the battery pack, either in or out, ever, for more than a few hundred ms. We might get that much during a short condition from a node, but shorts in nodes should be handled by the TPS chips on the RNH. For extreme circumstances, each LiPo cell has an internal 20 A fuse (of the same LittleFuse type) on a small board buried in each of the cells in the main battery pack. F100 is supposed to sit right in between these two regimes: it should blow first before any battery cell fuses, and only if the short is not handled by something else (e.g.,RNH circuit breaker).

### D100 OVP/RP protection diode - 20V unidirectional TVS SMB - LittleFuse SMBJ20A (DK SMBJ20ALFCT-ND)

**Purpose:** Cause a short circuit to blow F100 if the applied voltage to the pack is ever >> maximum pack voltage (OVP) or is reverse polarity (RP).

**Notes:** First, D100 must let the battery charge up to the pack's 16.8V maximum charge voltage. We should give it some volts of head room, especially since we might be charging up to 18V which might sneak in as some kind of transient. So we'll put the reverse stand off voltage at 20V, which then has a actual breakdown voltage of 22.2 - 24.5 V. If we get that high, something is wrong, and we should definitely blow. Also, if we ever hook this up backwards, D100 will instantly conduct causing F100 to blow. D100 must survive long enough to *allow* F100 to blow: the SMBJ20A is rated to handle a half sine wave peak of 100A @ 8.3 ms, which is plenty high curent and long enough to blow F100.

### C118,C115 filter caps - 100 nF @ 50 V 0603 (DK 445-6938-1-ND)

**Purpose:*** Absorb ESD and small transients and do some filtering on the PACK+ input.

**Notes:** No interesting properties except high voltage. There are two in series so if one fails short, you don't actually get a short on the wrong side of the fuse.

### C116,C117 filter caps - 100 nF @ 50 V 0603 (DK 445-6938-1-ND)

**Purpose:** Absorb ESD and small transients around the protection MOSFETs.

**Notes:** No interesting properties except high voltage. There are two in series so if one fails short, you don't actually get a short that bypasses the protection MOSFETs.

### R100 slow charge ("precharge") resistor - 249 ohms @ 500 mW 1% 1206 - Stackpole RNCP1206FTD249R (or DK 541-249UCT-ND)

**Purpose:** Slowly charge (limit the current) into the LiPo pack when it's very, very depleted. 

**Notes:** We want this because we will, inevitably, deplete the pack a couple of times on purpose or more likely not on purpose. Classically, you charge at 0.1C until the cell voltage rises to 2.8V. 0.1C is 400 mA, so with a charging voltage of 18V and a discharged pack of 2V/cell (the worst we've seen), that's 10V/400mA = 25 ohms. Power dissipation is 400mA^2 * 25 = 4 watts. That's a crazy big resistor, so let's reduce the resistance up by 10x which is 10V/250ohms = 40mA and power dissipation is 40mA^2 * 250 = 400 mW. Rounding up to 500 mW gives us a reasonable resistor, albeit with a very slow 0.01C charge rate. 

### Q100 slow charge ("precharge") switch - -30V Vds 0.5 mOhm P ch MOSFET - Vishay Siliconix Si2343DS-T1 (DK SI2343DS-T1-E3CT-ND)

**Purpose:** P channel MOSFET to turn on pre-charging.

**Notes:** At &lt;= 40 mA, we should have no problem with almost any P channel MOSFET, as long as it has a Vds rating of >= 30 V and matches the suggested transistor's maximum VGS(th) of 3V. There's a ton here, we'll choose an SOT-23 package and one with 0.0.086 ohms at Vgs = -4.5V which gives a power dissipation too low to care about during precharge. **FIXME:** CHECK THE PACKAGE.

### R101 normally off pullup - 1M 0603 (DK RHM1.00MCFCT-ND)

- Why is this 1M in the datasheets and EVM?

### D101 and D102 power supply diodes - Schotkey 0603 package (DK 478-7798-1-ND)

**Purpose:** Prevent bleedback inside of the BQ2060 from charger Vcc to battery Vcc and vice versa.

**Notes:** Should be Schotkeys? > 20V rating.

### R123 shunt resistor - 10mOhm 1% 1W - Vishary WSH2818R0100FEA (DK WSHA-.01CT-ND)

**Purpose:** Provide voltage drop for BQ3060 to measure the current from the battery (two quadrant).

**Notes:**

- The bq3060 takes between -0.2 to 0.25 V inputs across the SRP/SRN pins.
- From the data sheet: "using a 5 mΩ to 20 mΩ typ. sense resistor" and from the circuit discussion doc, "For a pack with two parallel cylindrical cells, 10 mΩ is generally ideal."
- The SenseResistor register in the bq3060 contains the value of the sense (shunt) resistor across SRP/SRN. It's set in uOhm, and it can be set from 0 to 65,535 uOhm. The default value is  10,000 uOhm which is 10 mOhm.
- The reference circuit description says "Tc < = 75 ppm in order to minimize current measurement drift with temperature".
- The EVM uses a 0.010 ohm, 1-W, 1%, Tc = 75ppm, 2512 resistor (Vishay WSL-2512-010).
- Let's choose 10 mOhm. We could go less, but then we drop voltage gain. We could go higher, but then we power disappation is a problem. 10 mOhm seems like a good engineering comprimise. Now, what power?
- 10 mOhm dissipates 160 mW @ 4A, 1 W @ 10 A and 2.25 W @ 15 A. 
- This means that we need 1W *at least* in order to not cook up if we have to run up to our fused limit.
- In a temporary short, we still need to beat the fuse. The 5 second time for the fuse is 40 A, so it ought to handle that.
- We choose the WSHA-.01CT-ND (Vishary WSH2818R0100FEA) because it's 5 W but still has a 99 W/in^2 rating, and has 45 A of overrating curent for 5 seconds. It's over-rated, but that's fine.

### TH100, TH101 Battery temperature thermistors - NTC 10K +/- 1% (DK 445-2554-1-ND)

**Purpose:** Measure the battery cell temperature to affect battery charging.

**Notes:**

- Recommended: Semitec 103AT, which are through-hole "NTC 10kohm 1%" thermisters. It's rated at R_25 = 10.0kOhm +/- 1% and B value = 3435K +/- 1%, Dissipation = 2mW/deg C, Thermal time constant = 15 s, -50 to +110 deg C
- Found TDK Corporation NTCG163JF103FT1 which is R_25 = 10k +/- 1%, B25/50=3380K, B25/85=3435K, -40°C ~ 125°C, in 0603.
- Use Vias or pinheader, and then we'll solder pigtail leads onto the thermister and bury them between B1 and B2 and B3 and B4.

### U100 battery fuel gauge and balancer - BQ3600 - (DK 296-25544-5-ND)

- TI BQ3060PW "SBS 1.1-compliant gas gauge and protection IC with CEDV" in a 24-Pin TSSOP
- **Purpose:** Monitor and balance the 4s1p 4.25 AHr Lithium Ion Polymer battery back. This is the best chip EVAR... some features:
   - Advanced CEDV (Compensated End-of-Discharge Voltage) Gauging
   - Full Array of Programmable Protection: Voltage, Current, and Temperature
   - Low Power Consumption Sleep Mode: &lt; 69 μA
   - Cell balancing (!!!!)
   - From the data sheet: "The bq3060 provides software 1st level and 2nd level safety protection on overvoltage, undervoltage, overtemperature, and overcharge, as well as hardware-overcurrent in discharge, short circuit in charge and discharge protection." Not too shabby.
- **Notes:** We're not using the suggested chemical fuse in the various datasheets.

## B100, B101A, B102A, B103A Lithium Ion Polymer batteries

- "AA Portable Power Corp" PL-5467100-2C Li-polymer cell
   - Fully discharged voltage: 2.75 V (= 11.00 V)
   - 3.7 V nominal (= 14.8 V)
   - Charge voltage: 4.20 ±0.03 V (paclk = 16.8 V)
   - 4250 mAh rated capacity 
   - ≤ 20 mΩ internal resistance
- **Purpose:** Duh.
- **Notes:** See the [[battery pack page|avionics/av3-battery-pack]]. 

## J100 RocketNet Battery Connector (DK 952-1933-ND)

- J100 = Harwin M50-3500742 low-profile pin header
- J100 mate on rocketnet connector = Harwin M50-3150742 low-profile bottom entry socket
- **Purpose:** This is a 1.27 mm (0.050 inch) 2 x 7 = 14 pin connector between the battery pack and the RocketNet Hub (RNH) board. The RNH has the STM32F407 microcontroller which talks I2C/SMBus to the BQ3060, as well as the BQ24725 SBS battery charger. The pins are:
   1. Pack +
   2. Pack +
   3. Pack +
   4. Pack +
   5. SCLK (SMBus clock)
   6. SCLK (SMBus clock)
   7. SDAT (SMBus data)
   8. SDAT (SMBus data)
   9. !PRSNT (Pack is plugged in)
   10. !PRSNT (Pack is plugged in)
   11. Pack -
   12. Pack -
   13. Pack -
   14. Pack -
- **Notes:** At about 1 A per pin, that's a 4A toal. Given our pack voltage of 10 - 16.8V, that's 40 - 67 W. We should be able to draw the 2-3 amps that the rocket takes without a problem. ISSUE: The M50-3150742 is *very* hard to get a hold of. It's not stocked by anyone, we may have to ask for samples.

## Input filtering and protection

Removed. On the EVM, a simple input filter to absorb ESD and spikey things.

## Q103,Q104 = Cell Balancing N Channel MOSFETS

- Stupid tiny package, but can't find or fit anything bigger: Vishay Siliconix SI1023X-T1-GE3 (DKSI1023X-T1-GE3CT-NDP)

## R105, R110, R116, R122 Cell balancing resistors - 0603 100 ohms 0.25 W (DK 541-100SCT-ND)

- **Notes:** 100 ohms across a fully charged 4.2 V LiPo battery should give us 176 mW of raw power... so 0.25W should be fine.

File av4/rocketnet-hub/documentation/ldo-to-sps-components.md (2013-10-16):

# Micrel MIC37101-2.1YM "1A Low-Voltage μCap LDO" to Murata LXDC55KAAA-205 "Micro DC-DC converter" Adapter board

Purpose: convert 3.3V to 2.1V @ 0.85A for the KSZ8999 Ethernet switch. Must be able to be turned on and off.

## MIC37101-2.1YM notes

- In:  +2.25V to +6V
- Out: 2.1 V +/- 1%
- En: high (2.25V) = enable, logic low (0.8V) or open = shutdown.
- FLG: Open-collector error flag output. Active low = output under voltage.
- Cout: 4.7 (min) to recomendded 10 uF
- Cin: 1 uF
- Dropout: 250 (typ) - 400 (max) mV at 0.75A

## LXDC55KAAA-205

- In: 2.7 to 5.5V
- Out: 0.8 to 3.6V @ 3 A +/- 2.5% 
- Out ripple: 20 mV max ripple, graph says 10 mV
- En: ON/OFF control pin H: Enable (1.0V), L: Disable (0.4V)
- PG: Output Power good output pin H: Normal Operation
- Cin: 10 uF recommended
- Cout: 22 - 150 uF recommended

## Capacitance on the RNH PCB

- Cin 
   - 1x 4.7uF 0603 (local)
- Cout
   - 1x 4.7uF 1206 (local)
   - 3x 100nF 0402 (local)
   - 5x 10uF 0603 (distributed)

Conclusion: bump up Cin 0603 to 10 uF and Cout 1206 to 22 uF and everything should work. Bonus points for adding more capacitance on the daughterboard, although this shouldn't be necessary.

## LXDC55KAAA-205 Feedback Resistor

Calculated from datasheet formula:

  Rfb = 5.44k/(2.1-.8)-1.6k = 2.584k

Using 1% E96 values, that's 2.55K

  Vout = 5.44/(2.55+1.6)+0.8 = 2.111 V

11 mV off is fine, that's &lt; 1 %. 0402 should be fine, and small enough to fit on the board.

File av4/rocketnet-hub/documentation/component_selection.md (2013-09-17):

# Rocketnet Hub Component Selection Guide

This document aims to explain the component selection for the "RocketNet Hub" (RNH) power and communications hub designed by the 2012-13 PSU ECE capstone team. The intention is to provide insight into the design decisions made where it might not be obvious ; there is no intention to provide the reader with a comprehensive design example that is suitable for any purpose other than exact replication. The target audience is expected to have design experience with microelectronics power distribution, modern physical layer communications designs, and understand matched impedance differential signaling.

Also, to fully understand these design decisions, see the requirements and specifications for this project here: <http://psas.pdx.edu/avionics/capstone2012/>

----------------------------------------------------------------------------------------------------------------------
# SCHEMATIC SHEET 1: Microcontroller (MCU)

## U1, MCU, ST Microelectronics STM32F407V100

For this project the MCU chosen was to not only to be used for our capstone design but also slated to replace the LPC2468 MCU used on the previous version Generic Front End (node4 GFE) boards. Thus despite a push from the capstone team to use an Atmel AV32 or Atmel ARM MCU it was decided by PSAS that an ST Micro STM32F407 MCU would be used. This microcontroller does offer some cost advantages over Atmel's offerings both in per unit cost and the cost of development tools. Given that PSAS is a cost conscious group that has ample expertise to draw from, the higher quality documentation offered by Atmel did not justify the added expense. Several Olimex STM32-E407 development boards where acquired and used by the PSAS software team to concurrently develop firmware for the RNH.

## Support Components

### Crystal (C106, C107, and X1 -- 8Y-25.000MEEQ-T)

The MCU has an internal oscillator circuit and can run without an external crystal. However, for Ethernet functionality the MII interface must operate at 25MHz +/- 50ppm. This is beyond the capabilities of the internal oscillator. Thus an external crystal must be used. The value that makes the most sense to the design team is 25MHz. By using this value we can avoid mucking around with the PLL resources of the MCU and still provide the required MII interface clock. Additionally, the MCU has two clock outputs and we can use one of these to buffer the crystal and use this same crystal to also drive the KS8999 Ethernet switch. The part selected is the 8Y-25.000MEEQ-T from TXC Corp. This crystal has a load capacitance rating of 10pF and a +/-10ppm frequency stability/tolerance. The load capacitors should be selected with 1% or less tolerance and C0G temp. coefficient or better.

### Bypass Caps

The supply pins of the MCU will each be provisioned one 0.1uF ceramic cap. X5R or X7R 0402 ceramic capacitors should be used. A bulk capacitor with a nominal value of between 10 and 22 uF should be placed near the MCU's 0.1uF bypass caps. The bulk capacitance value is not critical so any temp. coef. 0603 ceramic cap will work. The two crystal pins also require capacitors. For these two C0G ceramic 0402 capacitors should be used. The value should be 10pF.

### Analog Supply Filtering (E5)

The Analog supply pins were isolated with an 0603 ferrite bead to block digital switching noise. As the only analog resource used in the MCU was the ADC to monitor the current draws of both the battery and each node, this was likely an overly conservative addition to the board. During testing it is recommended that the ferrite bead be replaced with a 0 Ohm resistor. This will allow for a reduced BOM for future revisions of the board should it prove functional without this filter.

## Interfaces

### Reset Logic

The MCU has a reset signal that needs to be weakly pulled high during normal operation. This is accomplished by a 10kOhm resistor. The value is chosen to reduce power consumption when the line is pulled low. (Though given the length of time that this signal is ever likely to be held low it is a really rather pointless consideration. Any value from 100 to 100k could be used.) The MCU has internal power on reset and brownout detection circuitry and thus no external reset logic was added to ensure proper response to these conditions.

### JTAG (J22)

The MCU supports both programming and debugging through the ARM standard JTAG interface. This bus is broken out to a 2x5 50mil header. Signals used are the TMS, TCK, TDO, TDI, and MCU reset. For more information on these signals or the JTAG implementation used in the STM32F407 please see google.com

### Serial UART (J10)

To support realtime debugging and logging, a serial UART channel was broken out to a 1x4 50mil header. Signals preset are TXD and RXD, no flow control signals are present. This is a 3.3V interface with no protection. Care should be used to ensure that the USB to UART adapter used is configured for 3.3V or damage will likely result to the MCU, adapter, or both.

### MII

The MCU is connected to the Ethernet switch, discussed later, by two interfaces. The MII interface is the connection between the MAC and switch. The other interface is a serial interface and will be discussed below. The MII interface is an industry standard interface for connecting a MAC to a PHY. It is implemented per the standard with the exception that neither TX\_ERR or RX\_ERR are present. More information on this interface can be found via Goolge.com.

### I2C (J11, R15, R17)

    The I2C, or more properly TWI, interface is used to interface with the battery charger IC and fuel gauge IC. The MCU is the bus master. This is an open collector interface and thus requires the presence of a pull up resistor on each signal line. 2.2kOhm 0403 resistors were selected from past experience--no calculations or simulations were performed. If the bus fails at desired baud, please scope the bus at J? and look for excessive skew. If this is found, decrease the value of the pull ups. If reduction in power consumption is desired, these may be increased until such point as the bus begins to fail at max baud.

### Rocket\_RDY (Q1, U3)

The MCU is responsible for sending the final go signal to the launch tower signifying that the rocket is ready to launch. This is accomplished through a non-inverted signal buffered by a simple N-channel MOSFET. The signal is pulled high on the gate side and low on the source side. It is isolated from the MCU by the FET and protected by a 100Ohm resistor and parallel TVS diodes. The Capstone team wished to implement this signal differentially due to the 9m long cable that it must be sent over, but the cable had already been assembled. Future revisions of this board and the Launch Tower interface should explore further the benefits of differential signaling.

## Debugging

### RBG LED (LED37)

A single RGB LED was added to facilitate simple state display of the MCU. The implementation of the state machine and assignment of colors is left to the firmware team.

### Serial UART (J10)

A serial UART port is provided to facilitate realtime logging via print statements. The implementation of this functionality is left to the firmware team. Using the boot mode selection headers it is also possible to load a boot image over the UART port without flashing the internal memory. This can be used during initial code bring up to reduce time wasted writing images to flash. 

### JTAG (J22)

The STM32F407 supports JTAG programming and debugging. This is useful for stepping through code but is not appropriate for realtime debugging. This bus is intended only for initial programming and code bring-up.

### BOOT SEL (J5, J12)

The STM32F407 supports multiple boot sources and this can be selected by pulling the BOOT\_SEL pins either high or low. In conjunction with the UART port it is possible to load a boot image directly from a host computer without flashing the internal memory. This can be useful for initial code bringup. Please see the datasheet for boot configurations.

## System Monitoring

### Current Draw (U14, U15)

The MCU is configured to monitor the current draw of each connected node and the battery. This is accomplished through the internal ADC and two external analog multiplexers. At any time the MCU is monitoring one node from NODE\_1 through NODE\_4 and one node from NODE\_6 through NODE\_8, the only exception to the previous statement is that when monitoring NODE\_1, it is the only node monitored as there is no NODE\_5. The node currents are measured on NODE1\_4\_IMON and NODE5\_8\_IMON. Selection of the nodes to monitor is accomplished by setting the select bits IMON\_A0 and IMON\_A1. The battery's charge current is also monitored. This is present on BAT\_IMON. Use of this data is left to the firmware team, though possible uses would be to shut down a node if it is drawing unusually high or low amounts of current or determining if there is enough current sourcing capacity to turn on a given sub-system.

## System Control

### Ethernet Switch power supply and reset (C12, D1, Q8, Q9, R43, R65)

The MCU is responsible for enabling the Ethernet switch. This is done by asserting ETH\_EN. This will enable the switch's 2.1V LDO and access to 3.3V IO supply. Once both supplies stabilize, the MCU must boot strap the Ethernet switch using the SPI3 serial interface. This is a hack. The switch is designed to function as an I2C slave on a dedicated bus but the MCU only has a single I2C interface and that bus has other devices on it. The proper solution would have been to use a bi-directional tri-statable logic buffer to isolate the Ethernet switch from the rest of the I2C bus. However, the decision came down from PSAS to use the SPI interface. Implementation is left to the firmware team. The Ethernet switch can be reset without powering down its supplies by clearing ETH\_RST\_N. Note: this signal should not be tri-stated and driven to a known state prior to asserting ETH\_EN. Please note that C12 and R43 create a delay in ramping the 3.3V supply to allow the 2.1V core supply to come up first. D1 ensures 
that this supply is shut off quickly.

## Node Power

Each node can be turned on or off by the MCU. This is accomplished by clearing or setting (respectively) the NODEx\_!EN signal. In the case that a node draws more current than it is intended to and triggers the over-current protection system, the NODEx\_!FLT signal will be asserted. It is left to the firmware team to determine proper response to this signal.

-----------------------------------------------------------------------------------------------------------------------
# SCHEMATIC SHEET 2: Node Power Switches and Connectors

## TPS2420: 3-V to 20-V INTEGRATED FET HOT SWAP CONTROLLER (U7, U8, U9, U10, U11, U12, U13)

Each of the 7 nodes to be connected to this distribution board was to have its own power switch controlled by the MCU. After much debate the TPS2420 from TI was selected. This IC offered the design team many benefits though it also provided unnecessary functionality. Our main requirements for the node power switch were that it provides a high level of integration with no external components except small capacitors and resistors. An integrated FET was a must. Over current protection was also a must. The TPS2420 was selected by PSAS from TI's offering of hotswap power switches by PSAS. The justification was that it also included a soft current limit that could be exceeded for a limited time and the ability to externally set its reset behavior. The package size was also of utmost consideration. The TPS2420 comes in a standard QFN-16 with a DAP to dissipate heat. Several characteristics are dependent on the node being powered and the values of the resistors and capacitors that set them are left to PSAS to determine. The datasheet lists the formulas used to calculate each. Key settings for this chip are:

- Hard Current Limit (IMAX) (R51, R66, R67, R68, R69, R70, R71)
   - On top side of PCB near node connector for ease of change.
- Soft Current Limit (IFLT) (R121, R122, R123, R124, R125, R126, R127)
   - On top side of PCB near node connector for ease of change.
- Soft Limit Timer (CT) (C95, C96, C97, C98, C99, C100, C101)
   - On top side of PCB near node connector for ease of change.
- Reset Behavior: latch reset condition and wait for MCU to reset switch

Additionally, LED's were connected to the power good and fault signal lines, green and red respectively. These lines are common collector and thus pulled high by 10kOhm shunt resistors. The TPS2420's final benefit is a scaled version of the output current that is clamped to 2.5 V. This is used to drive an ADC channel on the MCU via an analog mux.

- IMON Resistor (R49, R52, R54, R56, R58, R60, R62) TBD
- Power Good LED (LED3, LED6, LED8, LED11, LED14, LED16, LED39) APT1608CGCK (Green 0603 V\_f 2.1V I\_d 20mA)
- Fault Cond. LED (LED2, LED4, LED7, LED10, LED12, LED15, LED18) APT1608EC (Red 0603 V\_f 2V I\_d 20mA)
- LED Current Limiting Resistors (R19, R23, R26, R30, R33, R36, R39, R50, R53, R57, R63, R107, R110, R112) 750 Ohm (1.6 mA - 1.73 mA)

## MAX4734: 0.8Ω, Low-Voltage, 4-Channel Analog Multiplexer (U14, U15)

The STM32F407V LQFP-100 lacks sufficient ADC inputs to simultaneously monitor the output current of all the nodes and the battery charger. The solution to this limitation was to either move to a larger package of the STM32F407 or add one or more analog muxes. The mux solution simplified routing and allowed for all the GFEs to use the same chip and package as the used for the distribution board. The specific mux chosen, Maxim's MAX4734, was selected for its small size (QFN-9) and very low Ron. The choice to use 2 4:1 muxes instead of one 8:1 mux was made to further simplify layout. The select bits for the muxes are shared meaning that at any given time the MCU is monitoring the charge current and two node currents, the only exception is IMON\_Ax = 2'b00 when only Node 1 is monitored as there is no Node 5. To simplify the firmware team's job slightly, a pull down was added to N1 of U15 to ensure that the value reported for the non-existent Node 5 is always in a known state.

- Bypass Capacitors (C10, C11)
- Standard IC bypass caps, 100nF
- Pull-down Resistors (R18)
- To account for the odd number of channels being multiplexed by the two MAX4734's one input of U15 is pulled low to provide a known value for that channel.

-----------------------------------------------------------------------------------------------------------------------
# SCHEMATIC SHEET 3: Power Supplies

The board is powered by a 4-cell LiPo battery pack. This works out to a nominal voltage of ~ 14.7 V under battery power and ~ 18 V under charging conditions. The MCU can run on 1.8 - 3.3 V. The design was intended to run on 3.3 V only initially. This became slightly more complicated after the selection of the KS8999 Ethernet Switch as this chip requires a 2.1 V core voltage. While the 3.3 V supply should be always on, the 2.1 V supply was required to be off initially and powered on when the KS8999 was enabled by the STM32.

## U5, LTM8023 (2A, 36V DC/DC Step-Down μModule Regulator)

The LTM8023 uModule from Linear Technologies was selected for its high level of integration and low external part count. The LTM8023 is capable of sourcing up to 2 A of regulated power with an efficiency of 80%+. As the KS8999 requires 1 A just by itself the 2 A 3.3 V supply seemed reasonable to source its LDO and the remaining logic. 

- Vout: 3.3 V
- Osc. Freq.: 650KHz
- Sync. Freq.: 650KHz -- set by MCU's timers (crystal locked)
- `R_T` (R74) 49.9KOhm
- `R_ADJ` (R73) 154KOhm
- `C_in` (C103) 2.2uF (0805)
- `C_out` (C104) 22uF (1206)
- `PGOOD` LED (LED22) APT1608CGCK (Green 0603 `V_f` 2.1V `I_d` 20mA)
- LED Current Limiting Resistor (R128) 750 Ohm (1.6 mA)
- `EN`: Tied to supply voltage, Always on

FIXME: C104 is specified as 22μF 1206  but in the schematic is specified as 2.2 uF 0603.

## U6, MIC37101-2.1YM (2.1 V 1A Low-Voltage μCap LDO)

The Micrel MIC37101 line of LDO's was selected to source power to the KS8999. According to the datasheet, the KS8999 draws (,640,850) mA in 100BASE-TX operation, so a max supply current of 1 A was chosen. The MIC37101-2.1YM is a fixed voltage LDO with a typical maximum output rating 1.6 A. This is  sufficient to drive the KS8999 with reasonable headroom to account for potential variation. All resistor values were chosen from each manufacturer's datasheet (with the exception of the LED current limiting resistor R128). The capacitors chosen for the Micrel MIC37101 were the minimum value recommended in the datasheet necessary to ensure stability. Power dissipation is (3.3 - 2.1)* 0.85 = 1.02 W of power.

FIXME: WHAT?! 1W dissipation in an LDO?! That's **CRAZY**. How did we miss this? This MUST be a SPS. In the next redesign, it's clear that the LTM uModule should have two outputs, where the second one can be sequenced independently of the first. Can we fix the current board? With a maximum drop out of 280 mA, we might be able to lift the Vin pin and power it off an SPS at 2.5 V - that's a dissipation of (2.5 - 2.1) *.85 = 340 mW. That's still a lot. Better to directly replace it with some kind of 3.3 V to 2.1 V module: at 90% efficiency for a dissipation of 10x less, ~ 100 mW. For example, A Murata LXDC55KAAA-205 could be used on a carrier board with one external feedback resistor to make a > 90% SPS in the same footprint as the SOIC8 of the MIC37101. It needs a daughterboard, however, to adapt the LGA to the SOIC18. It might want more capacitance, too. 

- EN: Weakly pulled to logic 0, controlled by U1.ETH_EN
- `C_in` (C52) 47uF
- `C_out` (C84, C85) 4.7uF, 0.1uF

----------------------------------------------------------------------------------------------------------------------
# SCHEMATIC SHEET 4: Ethernet Switch

## U4, Ethernet Switch, Micrel KSZ8999

The design requirements dictated that the switch chosen must have at least 7 ports. Furthermore, we were restricted from using any Broadcom SoC due to the company's exclusive access model. This left us with only Micrel's offerings to work with. The KS8999 had the added benefit of an MII interface to the MCU which allowed the design to avoid adding any discrete PHY IC's. It also met the design requirements by offering 8 ports with integrated PHYs and one MII digital interface. The Micrel KS8999 development board was acquired to test potential configurations so that these settings could be set on the first run of the PCB. The settings used are:

* MIIS: 2b'X1 (reverse MII mode)
* MODESEL: 4b'0000 (LED mode 0)
* CFGMODE:1b'0 (I2C Bootstrap)
* LED[8][3]:1b'0 (AutoMDIX)
* Supporting Components

## Voltage Supplies (C12, D1, Q8, Q9, R43, R65, U6)

The KS8999 required a 2.1 V core and analog IO voltage. This is not a voltage that would otherwise have been provided on the board and thus an LDO was selected to do so. Please see Power Supplies for additional design decisions related to this LDO. There IO logic requires 3.3V to match the digital IO on the MCU. The 3.3V must ramp after the 2.1V supply. To accomplish this, a RC delay circuit and PMOS power switch was implemented. The diode (D1) allows for this to be shut down without waiting for the RC delay circuit to discharge.

## Bypass Caps

The supply pins of the KS8999 will each be provisioned one 0.1uF ceramic cap. X5R or X7R 0402 ceramic capacitors should be used. Bulk capacitors with a nominal value of  10uF should be placed near the KS8999's 0.1uF bypass caps. The bulk capacitance value is not critical so any temp. coef. 0603 ceramic cap will work. 

## Pull Up/Down Resistors (R2, R3, R4, R6, R7, R8, R10, R13, R14, R72, R116, R117, R118, R119, R120)

Several of the pins on the KS8999 must be pulled to either Vdd or GND to place the IC in normal operating mode. This is accomplished with 0402 0 Ohm resistors. The interested reader should consult the datasheet for further information on the effect of these pull downs. R72 is present as the MCU MAC's interface does not provision a TX\_ERR signal and thus it is tied low on the PHY side. Additional resistors are used to set MIIS, MODESEL, and CFGMODE. These configurations are described in the datasheet.

## Reset Circuitry (D2, D3)

The KS8999's reset is not 3.3 V tolerant and thus diodes and pull up resistors must be used to ensure safe operation. The circuit is provided in the data sheet. 0402 10k resistors should be used to minimize power dissipation. Any tolerance value may be selected. The diodes are SOT-23 to minimize size. The forward voltage should be minimized to ensure the reset line can be pulled low enough to be read as a logic 0. Schottky diodes are optimal for this purpose. The CDBQR0130L from Comchip Tech was selected for this purpose.

## Signal LEDs (LED1, LED5, LED9, LED13, LED17, LED21, LED25, LED29, LED33)

Each port provisions up to four signaling LEDs to denote the current state of the port. 0402 LEDs will be used with a nominal ID of 1mA. As each node will have two power indicators, green for power good and red to indicate a fault condition, yellow/amber seems the most reasonable choice for the Ethernet status indicators. PSAS determined that only one status LED per port needed to be placed. The part number selected for this component is VLMY1500-GS08 from Vishay. Forward voltage is 2V.

## Magnetics (Chokes: L2, L3, L4, L5, L6, L7, L8, L9, L10, L11, L12, L13, L14, L15, L16, L17 Transformers: T4, T5, T6, T7, T8, T9, T10, T11, T12, T13, T14, T15, T16, T17, T18)

The physical layer of the Ethernet specification (for copper) requires that the PHY's on either side of the connection be AC coupled to each other. To accomplish this, purpose-build magnetic transformers from Pulse were selected by PSAS and tested on the dev board. Additionally, common-mode chokes were also added to improve signal integrity. The transformers are quite large components and much effort was put into attempting to use capacitors to AC couple the connection and save space. This proved fruitless and transformers were instead used. The exact reason for failing to successfully couple with capacitors is unknown and further research for future revisions of the board should be considered.

----------------------------------------------------------------------------------------------------------------------
# SCHEMATIC SHEET 5: Off RNH Connectors

## J9 Battery Connector

Purpose: Runs high current power at Vbat from the 4S1P LiPo battery pack to the rest of the avionics system. 

- Vbat = (10,14.7,16.8) V. Leads are quadrupled-up to reduce power drop.
- SCL/SDA are SMBus connections to the battery pack, which should have a BQ3060 battery monitor on it.
- !PRSNT is a signal to the BQ3060 that the battery pack is actually plugged into a system (might be better called WAKE).

## J14 Umbilical Cord Connector

Purpose: Connects to the "umbilical cord" which connects to the Launch Tower Computer (LTC). Provides shore power and shore communications

- Power leads are "shore power" that power the rocket and charge the battery while on the pad. Shore power = (18,19,20)V. Quadrupled-up to reduce power drop.
- RocketReady is a safety-critical signal in the motor ignitor path that indicates to an indpendent relay in the LTC that the rocket is ready for flight.
- TX/RX are Ethernet data lines that connect the RNH and rest of the avionics system to the outside world. This usually means to a standard Ethernet switch and a bunch of laptops during testing and development. For launch, this connection is specifically between the avionics system and the LTC.

----------------------------------------------------------------------------------------------------------------------
# SCHEMATIC SHEET 6: BATTERY CHARGING BLOCK

## U2, Battery Charger, BQ24725

The onboard battery charger had been selected by PSAS prior to the beginning of the capstone project and was presented to the capstone team as a black box solution. Integration of the dev board's circuit with minimal adjustment was requested. The interested reader is directed to the datasheet and dev board user's guide for more information on this subsystem. Connections to the black box are I2C(<->), BAT\_IMON(->), external DC power(<-), Battery power(<-), and +18V(->). All internal signals are replicated per the dev board. Most components selected are per the dev board's BOM.

## In-Rush Limiter (R11, C60)

The two 3.9 Ohm 0.5W resistors from the evaluation board were replaced with a single 2 Ohm 1 W resistor. The 2512 size was selected because it was the smallest available component.

NOTE: Page 29 of the data sheet recommends a RC filter for VCC in order to prevent inductive kick from hot-plug events destroying the IC. This was NOT implemented, and probably ought to have been since out shore power cable is so long.

## Transient Voltage Suppression (D5)

A reverse biased TVS diode (SMAJ18CA) was added to protect against over-voltage. 20V voltage breakdown was chosen for the diode based on +18V Vin shore power.

## Enable (EN) Circuitry

Removed the optional enable/disable circuitry on VCC which causes board to be always-on when plugged into a power source.

## Various Capacitors

Sizes determined by component availability of 40V caps: &gt;10uF = 1206 / &gt;2.2uF 0805 / &gt; 1uF = 0603 / &lt;1uF = 0402

## Reverse Input Voltage Protection (Q6, R132, R133)
 
These components provide system and IC protection from reversed shore power (Vin) voltage. In normal operation, Q6 is turned off by negative Vgs. If the adapter voltage is reversed, Q6 Vgs is positive. As a result, Q6 turns on to short gate and source of Q2 so that Q2 is off. The Q2 body diode in reverse biased orientation blocks negative voltage from traversing into the system. However, CMSRC and ACDRV pins need R10 and R11 to limit the current due to the ESD diode of these pins when turned on. Q6 has a low Vgs threshold voltage and low Qgs gate charge so it turns on before Q2 turns on. R10 and R11 must have enough power rating for the power dissipation when the ESD diode is on, again these were selected based on the datasheet.

## Negative Output (BAT) Voltage Protection (R144, R143)

Selected as noted in the datasheet: If the battery pack is inserted backwards into the charger output (BAT) during production or there is a hard short on the battery to ground, it will generate a negative output voltage on the SRP and SRN pins. Built in IC internal electrostatic-discharge (ESD) diodes from GND pin to SRP or SRN pins and two anti-parallel (AP) diodes between SRP and SRN pins can be forward biased and negative current can pass through the ESD diodes and AP diodes when output has negative voltage. These two resistors for SRP and SRN pins are inserted to limit the negative current level when output (BAT) has negative voltage. The recommended resistor values of 10 Ohm (R144) for SRP pin and 7.5 Ohm (R143) for SRN pin were used.

## Inductor (L1)

We used the datasheet suggested value for the inductor, L1, 4.7uH. The bq24725 has three selectable fixed switching frequencies, the higher switching frequency allows the use of smaller inductor and capacitor values. The bq24725 has charge under current protection (UCP) by monitoring charging current sensing resistor (R134) cycle-by-cycle. Details on calculations for L1 and R134 are in the bq24725 datasheet, page 27. We used the suggested value of 10mOhm for the charging current sensing resistor (R134).

## Input (C39, C43) and Output (C119, C120) Capacitors

Input (C39 and C43) and Output (C119 and C120) Capacitors based on datasheet, with detailed calculations on page 27 of datasheet.

## Power MOSFETs (Q2, Q3, Q5)

Power MOSFETs Selection (Q2, Q3 and Q5) detailed calculations on page 28 of datasheet.

## `ACDET` divider (R137, R138)

`V_in`(shore power) is considered valid when `ACDET` pin is between 2.4V to 3.15V. R137/R138 as originally designed form a voltage divider with a diver coefficient of 0.134 (66.5 kohm and 430 kohm) which means valid shore power ranges from 17.91 to 23.5 V.

FIXME: Both the low and high end of ACDET are unecessarily high; anything &gt; 16.8V (the maximum battery voltage) should be OK. With an extra 200 mV of headroom and using the maximum 2.424 V cutoff, that is 2.42 / 17 = 0.142. Changing R137 only, 0.142 implies R137 = 71.37 KOhm -> 71.5KOhm.  R137 = 71.5 Kohm then sets the valid ACDET voltage range from 16.83 to 22.1 V, which is a better range.

## `ILIM` divider (R142, R139, C122)

The charge current limiter takes the lower of the voltage set by ChargeCurrent(), and voltage on `ILIM` pin. R142/R139 set a voltage divider to set `V_ILIM` which is 3.3V * 100k/(100k+316k) =  3.3V * 0.240 = 0.793 V. From the datasheet, `V_ILIM` = 20 * Ichg * Rsr --> Ichg = `V_ILIM`/(20*Rsr) = 0.793/(20*0.010) = 3.966 A. So, just like Figure 1 in the datasheet, it's set to 4A. This is probably fine: 4A seems like a fine upper limit on charge current, we'll most likely be running much lower than that.

Note that C122 seems gratuitous; it's not in the datasheet, and it probably doesn't need to be filtered. That said, it's probably not going to hurt anything and my filter some noise out.

## `IOUT` output (C110)

Either 20x the adapter current (shore power current) or 20x the battery charge current, selectable with SMBus command ChargeOption(). 

Datasheet says "A 100pF capacitor connected on the output is recommended for decoupling high-frequency noise. An additional RC filter is optional, if additional filtering is desired. Note that adding filtering also adds additional response delay.". 

ISSUE: it's probbaly not totally necessary, but that seems like a good idea.

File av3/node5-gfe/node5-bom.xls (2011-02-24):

Qty | Value | Type | Device | Parts | Vendor
1 | 2pF | C | C-EU0603-B-NOSILK | C2104
2 | 18p | C | C-EU0603-B-NOSILK | C2203, C2204
2 | 22p | C | C-EU0603-B-NOSILK | C2206, C2207
1 | 33p | C | C-EU0603-B-NOSILK | C2209
1 | 39p | C | C-EU0603-B-NOSILK | C2208
1 | 680p | C | C-EU0603-B-NOSILK | C2008
1 | 10n | C | C-EU0603-B-NOSILK | C2200
1 | 10n 50V | C | C-EU0603-B-NOSILK | C2011
1 | 15n | C | C-EU0603-B-NOSILK | C2004
1 | 68n | C | C-EU0603-B-NOSILK | C2100
16 | 100n | C | C-EU0603-B-NOSILK | C2007, C2102, C2103, C2201, C2202, C2205, C2210, C2211, C2212, C2213, C2214, C2215, C2216, C2217, C2218, C2219
1 | 100n 50V | C | C-EU0603-B-NOSILK | C2000
1 | 220n | C | C-EU0603-B-NOSILK | C2009
1 | 330n 50V | C | C-EU0603-B-NOSILK | C2002
1 | 1u 50V | C | C-EU0805-B-NOSILK | C2006
1 | 2.7u | C | C-EU0603-B-NOSILK | C2003
3 | 10u | C | C-EU0805-B-NOSILK | C2101, C2105, C2108
1 | 10u 50V | C | C-EU1206-B | C2005
1 | 22u | C | C-EUC1210 | C2010
1 | 22u 50V | C | CPOL-USD/7343-31R | C2001
4 | CDSU101A | D | DIODE_SILICON-0603 | D2001, D2200, D2201, D2202
1 | MA2Q705 | D | MA2Q705 | D2100
1 | PDS340 | D | D_PDS340 | D2002
1 | 2.0A Fast | F | FUSE1206 | F2000
1 | DEBUG-CONNECTOR | J | DEBUG-CONNECTOR | J2204 | JST
1 | ROCKETBUS | J | ROCKETBUS | J2000 | JST
1 | CMS1 | L | COIL_CMS1 | L2000
1 | EXC-CET471U | L | FILTER_EMI-EXC-CET | L2200
1 | FILTER_EMI-EXC-CET | L | FILTER_EMI-EXC-CET | L2201
1 | L_DR74-6R8-R | L | L_DR74-6R8-R | L2001
1 | L_NR4018T2R2M | L | L_NR4018T2R2M | L2100
1 |  | LED | LED_RGB_PLCC-6 | LED2200
1 | LED-GRN- | LED | LED-GRN- | LED2101
1 | RED | LED | LEDCHIP-LED0603 | LED2100
4 | PMV45EN | Q | PMV45EN | Q2000, Q2002, Q2200, Q2201
2 | SI7123DN | Q | P-MOS_SI7123DN | Q2100, Q2101
1 | Si7309DN | Q | P-MOS_SI7123DN | Q2001
3 | 0 | R | R-US_0603-B-NOSILK | R2215, R2216, R2217
1 | 0.033 | R | R-US_0805-B-NOSILK | R2003
2 | 33.2 | R | R-US_0603-B-NOSILK | R2209, R2210
3 | 100 | R | R-US_0603-B-NOSILK | R2108, R2211, R2212
1 | 660 | R | R-US_0603-B-NOSILK | R2101
6 | 1k | R | R-US_0603-B-NOSILK | R2004, R2102, R2107, R2111, R2205, R2206, R2207
1 | 1.5k | R | R-US_0603-B-NOSILK | R2208
1 | 1.6k | R | R-US_0603-B-NOSILK | R2105
5 | 10k | R | R-US_0603-B-NOSILK | R2002, R2006, R2012, R2112, R2202, R2203, R2213, R2214
1 | 15k | R | R-US_0603-B-NOSILK | R2104, R2008,
1 | 18k | R | R-US_0603-B-NOSILK | R2201
1 | 26.7k | R | R-US_0603-B-NOSILK | R2009
1 | 34.0k | R | R-US_0603-B-NOSILK | R2005
1 | 61.9k | R | R-US_0603-B-NOSILK | R2001
3 | 100k | R | R-US_0603-B-NOSILK | R2000, R2011, R2100
1 | 121k 1% | R | R-US_0603-B-NOSILK | R2103
1 | 200k | R | R-US_0603-B-NOSILK | R2110
1 | 500k | R | R-US_0603-B-NOSILK | R2007
1 | 532k | R | R-US_0603-B-NOSILK | R2010
1 | 1.0M | R | R-US_0603-B-NOSILK | R2109
1 | 100k @25C | RT | R-US_0805-B-NOSILK | RT2100
2 | SN65220DBVR | TVS | IC_SN65220 | TVS2200, TVS2201
1 | TVS_SMB | TVS | TVS_SMB | TVS2000
1 | 74LVC3G14DCU | U | 74LVC3G14DCU | U2202
1 |  | U | 741G74-VSSOP8 | U2102
1 | LPC2368 | U | IC_LPC2368 | U2200
1 | LT3972 | U | IC_LT3972 | U2002
1 | LTC4085 | U | IC_LTC4085 | U2100
1 | MAX5902AAEUT | U | IC_MAX5902 | U2000 | Maxim
1 | SN65HVD235 | U | IC_SN65HVD235 | U2201 | Mouser
1 | SN74LV163A | U | IC_SN74LV163A | U2203
1 | TPS63000 | U | IC_TPS63000 | U2101
1 | TLV3012AIDBVT | U | IC_TLV3012 | U2001
1 | 12.0 MHz | X | XTAL_CS10 | X2201
1 | 32.768 kHz | X | XTAL_CM415 | X2200

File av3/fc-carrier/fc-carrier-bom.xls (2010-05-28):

Qty | Value | Device | Parts | Distributor | Part Number | Qty needed | In Stock | To order | Notes
3 | NP | C-EU0603-B-NOSILK | C1020, C1033, C1034 | - | - | 0 | 0 | 0
2 | 22p | C-EU0603-B-NOSILK | C1000, C1007 | Digi-Key | 445-1273-1-ND | 4 | 0 | 4
2 | 200p | C-EU0603-B-NOSILK | C1002, C1009 | Digi-Key | 490-1434-1-ND | 4 | 0 | 4
4 | 15n | C-EU0603-B-NOSILK | C1011, C1013, C1045, C1046 | Digi-Key | 478-1359-1-ND | 8 | 0 | 8
1 | 82n | C-EU0603-B-NOSILK | C1029 | Digi-Key | PCC1761CT-ND | 2 | 0 | 2
13 | 100n | C-EU0603-B-NOSILK | C1018, C1019, C1021, C1028, C1030, C1031, C1032, C1035, C1036, C1039, C1040, C1041, C1042 | Digi-Key | 709-1101-1-ND | 26 | 100 | 0 | ADG in stock
1 | 330n | C-EU0805-B-NOSILK | C1006 | Digi-Key | 490-3327-1-ND | 2 | 0 | 2
2 | 2.7u | C-EU0603-B-NOSILK | C1010, C1012 | Digi-Key | 399-3127-1-ND | 4 | 0 | 4
4 | 10u | C-EU0805-B-NOSILK | C1003, C1004, C1043, C1044 | Digi-Key | 445-3448-1-ND | 8 | 100 | 0 | ADG in stock
1 | 22u | CPOL-USD/7343-31R | C1005 | Digi-Key | 399-3782-1-ND | 2 | 0 | 2
4 | 100u | CPOL-EUD/7343-31R | C1001, C1008, C1017, C1038 | Digi-Key | 478-4977-1-ND | 8 | 0 | 8
4 | DIODE-0603 | DIODE-0603 | D1000, D1001, D1003, D1004 | Digi-Key | 641-1002-1-ND | 8 | 0 | 8
1 | 2.0A Fast | FUSE1206 | F1000 | Digi-Key | 1206SFF300F/32CT-ND | 2 | 0 | 2
1 | ROCKETBUS | ROCKETBUS | J1001 | JST | 16PS-JED | 2 | 0 | 2 | Samples ordered from JST website
1 | TELEMETRY | 08PS-JED | J1002 | JST | 08PS-JED | 2 | 0 | 2 | PSAS in stock?!
1 | JTAG | 2mm pin header 2 x 6 | J1003 | Digi-Key | WM18839-ND | 2 | 2 | 0
2 | ETHERNET | Ethernet connector | J1007, J1008 | - | - | 4 | 20 | 0 | ADG in stock
1 | CMS1 | Choke | L1000 | Digi-Key | 513-1115-1-ND | 2 | 0 | 2
1 | RGB | OSRAM RGB LED | LED1002 | 475-2855-2-ND | 2 | 2 | 100 | 0 | ADG in stock
8 | RED | 0603 LED | LED1003, LED1004, LED1005, LED1006, LED1007, LED1008, LED1009, LED1010 | Digi-Key | 475-1195-1-ND | 16 | 100 | 0 | ADG in stock
1 | GRN | 0603 LED | LED11011 | Digi-Key | >????? | 2 | 100 | 0 | ADG in stock
1 | ZXMP6A17KTC | DPAK P-CH MOSFET | Q1000 | Digi-Key | ZXMP6A17KTCDICT-ND | 2 | 100 | 0 | Called Cascade Tech
5 | PMV45EN | SOT23 N-CH MOSFET | Q1001, Q1002, Q1003, Q1004, Q1005 | Digi-Key | 568-2356-1-ND | 10 | 100 | 0 | ADG in stock
1 | NTR4101P | SOT23 P-CH MOSFET | Q1006 | Digi-Key | NTR4101PT1GOSCT-ND | 2 | 100 | 0 | ADG in stock
2 | NP | R-US_0603-B-NOSILK | R1024, R1025 | - | - | 0 | 0 | 0
3 | 0 | R-US_0603-B-NOSILK | R1015, R1027, R1028 | Digi-Key | P0.0GCT-ND | 6 | 100 | 0 | ADG in stock
1 | 0.06 | R-US_0805-B-NOSILK | R1002 | Newark | 77M9489 | 2 | 0 | 2
3 | 22 | R-US_0603-B-NOSILK | R1056, R1096, R1099 | Digi-Key | P22GCT-ND | 6 | 0 | 6
26 | 33 | R-US_0603-B-NOSILK | R1016, R1017, R1019, R1020, R1047, R1049, R1050, R1051, R1052, R1053, R1054, R1057, R1058, R1059, R1060, R1061, R1062, R1063, R1064, R1065, R1066, R1067, R1068, R1094, R1095, R1097 | Digi-Key | P33GCT-ND | 52 | 0 | 52
4 | 82 | R-US_0603-B-NOSILK | R1040, R1055, R1098, R1100 | Digi-Key | P82GCT-ND | 8 | 0 | 8
9 | 470 | R-US_0603-B-NOSILK | R1029, R1030, R1031, R1032, R1033, R1034, R1035, R1036, R1046 | Digi-Key | P470HCT-ND | 18 | 0 | 18
2 | 2.32k | R-US_0603-B-NOSILK | R1037, R1038 | Digi-Key | P2.32KHCT-ND | 4 | 0 | 4
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

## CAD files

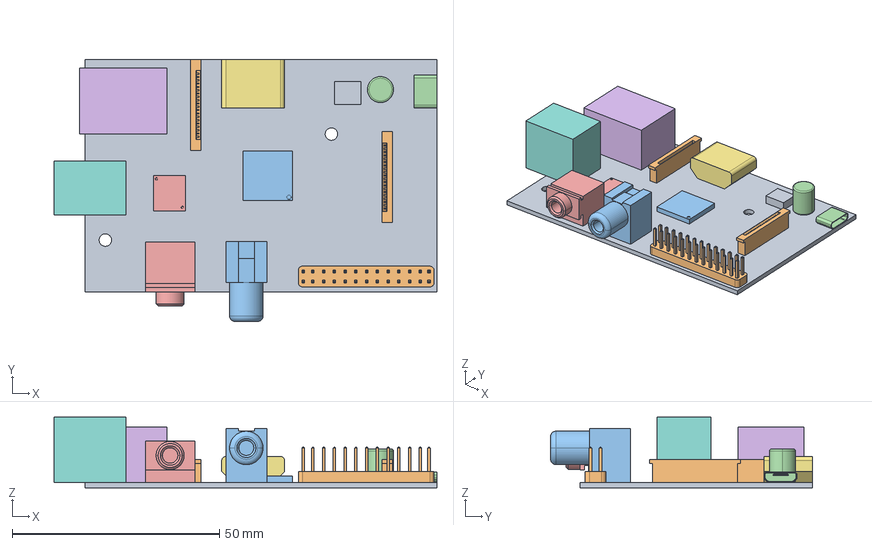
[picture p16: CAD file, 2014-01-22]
av4/raspi-camera/datasheets/modelb_assembly.stp
92.5 x 63.3 x 17.1 mm
BOARD
CAMSLOT_CONNECTOR x 2
CPUGPU
MICRO_USB_POWER_CONNECTOR
AUDIO_CONNECTOR
ETHERNET_CONNECTOR
HDMI_CONNECTOR
USB_2
POWER_MOSFET
PANNEL_CONNECTORS
DISPLAY_CONNECTOR
CAPACITOR
MEMORY_CHIP

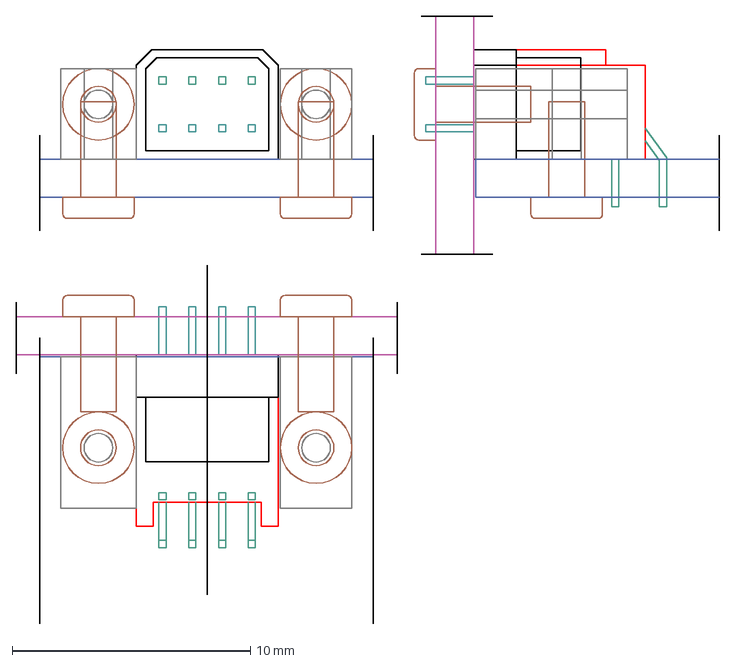
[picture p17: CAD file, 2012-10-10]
av3/rocketbus-connector/4-pin-rocketbus.dxf
29.5 x 25.5 mm

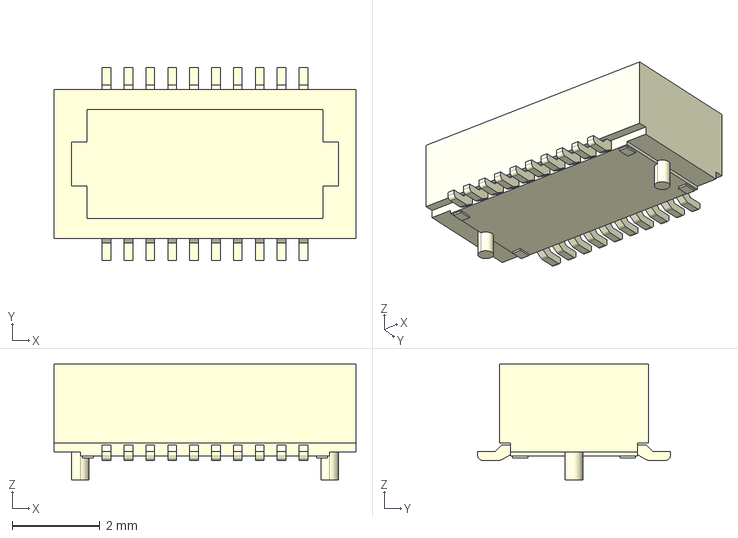
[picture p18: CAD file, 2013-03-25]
av3/rocketbus-connector/CAD/parts/JMC_connector_male.part.step
6.90 x 4.40 x 2.65 mm

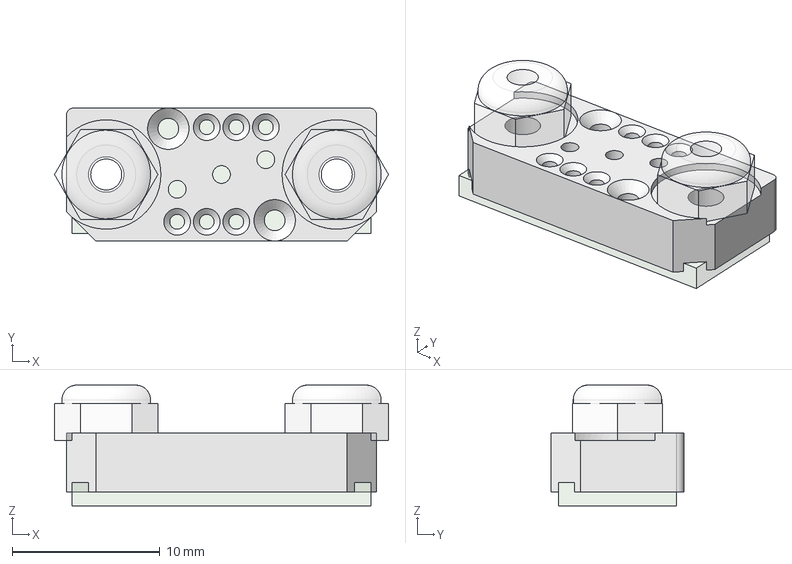
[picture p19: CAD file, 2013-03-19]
av3/rocketbus-connector/CAD/rockebus.assem.fcstd
22.6 x 9.00 x 8.18 mm
Nylock001
Nylock002
AdapterBoard_screwholes002
TopBracket

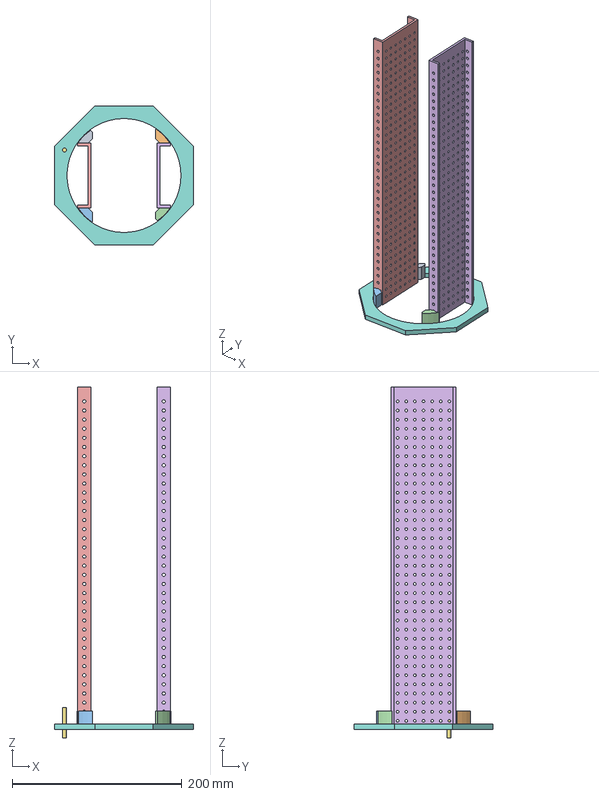
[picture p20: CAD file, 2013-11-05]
av4/avionics-rings/avionics-rings.fcstd
164.0 x 164.0 x 413.0 mm
Dbock001
Dbock002
Dbock003
Dbock004
Channel001
Channel002
Bolt
Holder

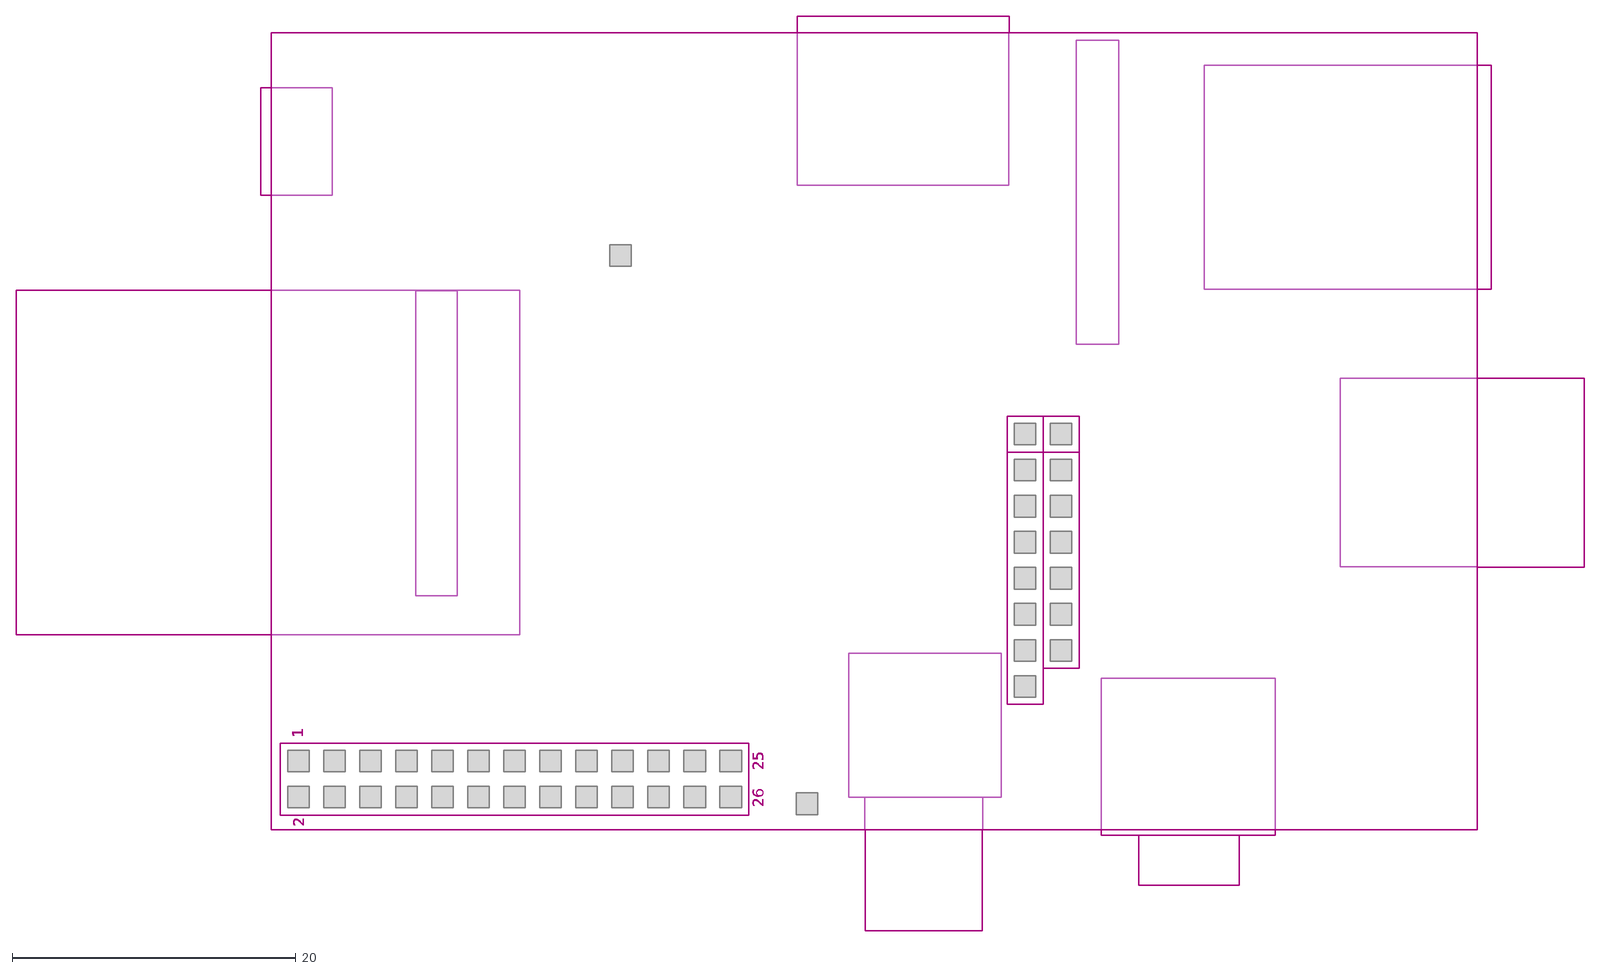
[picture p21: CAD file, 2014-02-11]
av4/raspi-camera/datasheets/ibex_rpi_model_b_v1_00.dxf
26
25
2
1

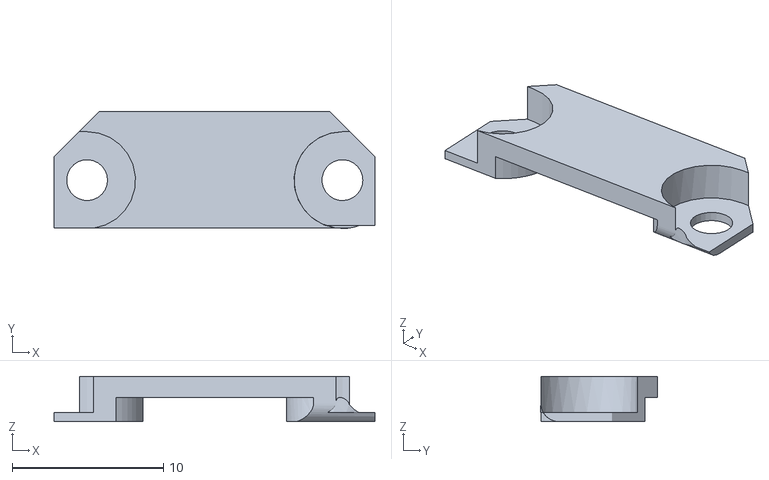
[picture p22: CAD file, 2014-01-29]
av4/rocketnet-connector/3d/print/top_RA_18.stl
21.2 x 7.72 x 3.00

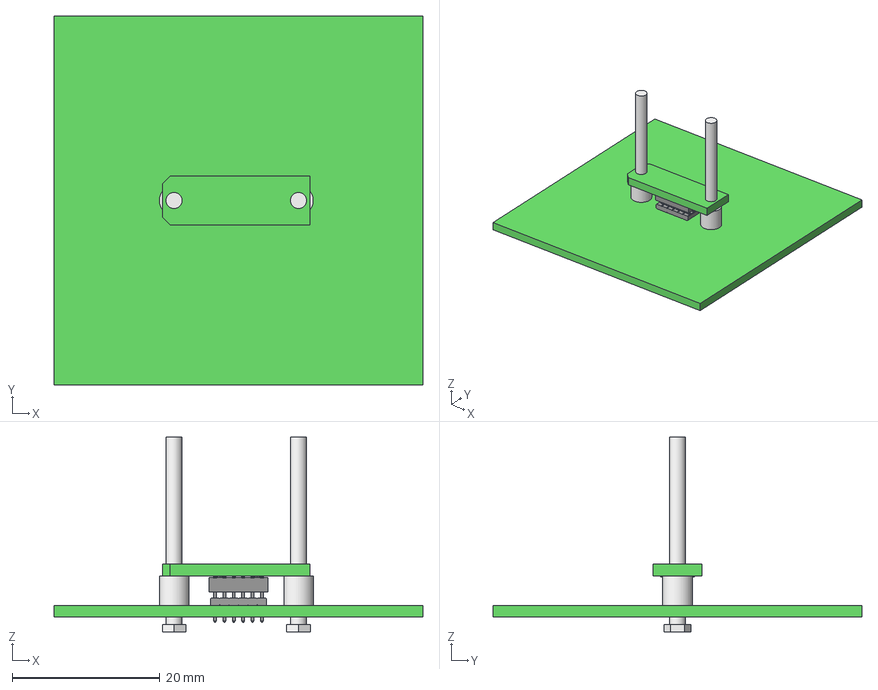
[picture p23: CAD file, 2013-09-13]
av4/rocketnet-connector/3d/rocketnet-connector-18pin.assemb.fcstd
50.0 x 50.0 x 26.4 mm
Base_CircuitBoard
Female_Header_12pin
Male_Header_12pin
screw_1
screw_2
standoff_1
standoff_2
Daughter_board

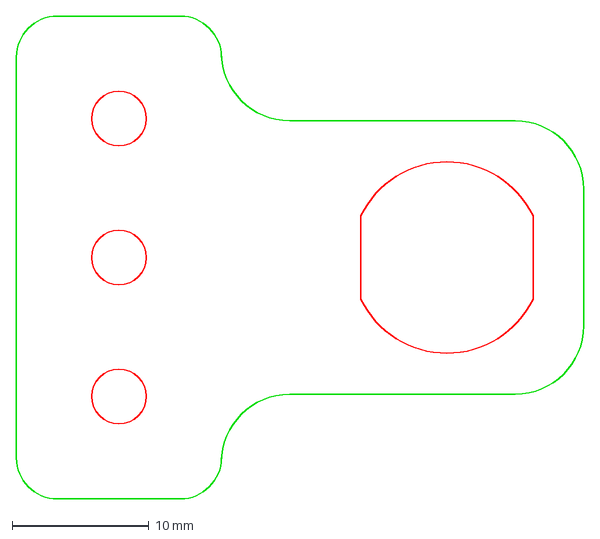
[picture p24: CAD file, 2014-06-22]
av4/umbilical/debug-umbilical-bracket.dxf
41.5 x 35.3 mm

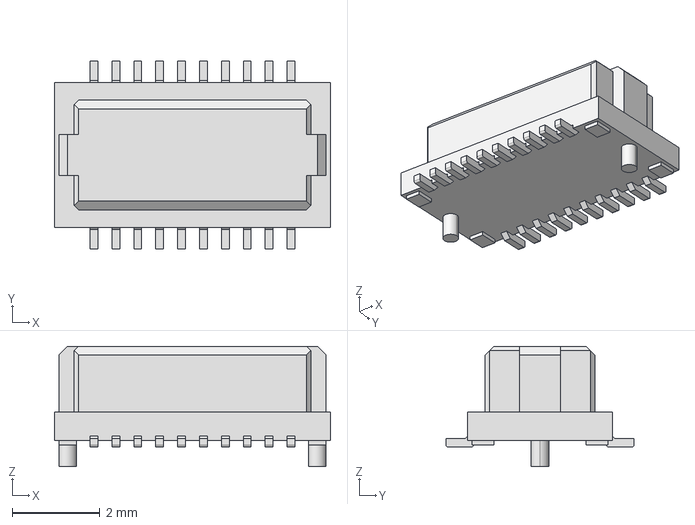
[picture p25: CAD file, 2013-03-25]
av3/rocketbus-connector/CAD/parts/JMC_connector_female.part.step
6.30 x 4.30 x 2.75 mm

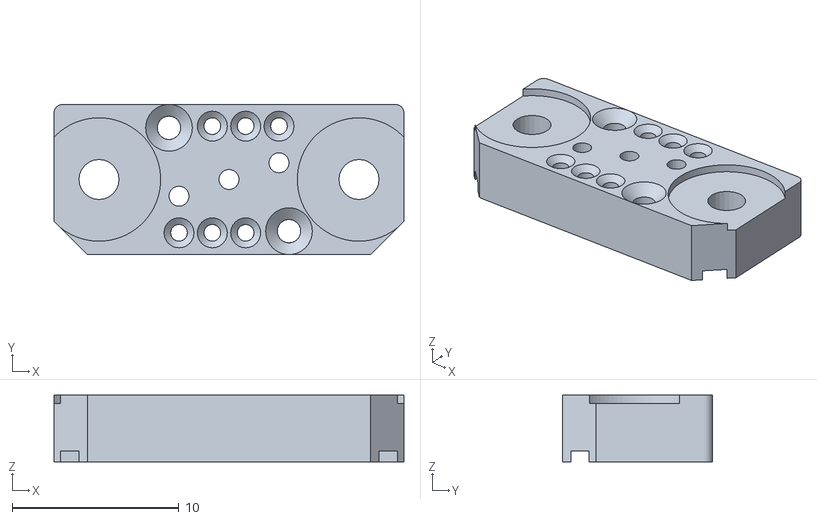
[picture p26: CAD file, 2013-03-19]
av3/rocketbus-connector/CAD/Top_Bracket.stl
21.0 x 9.00 x 4.00

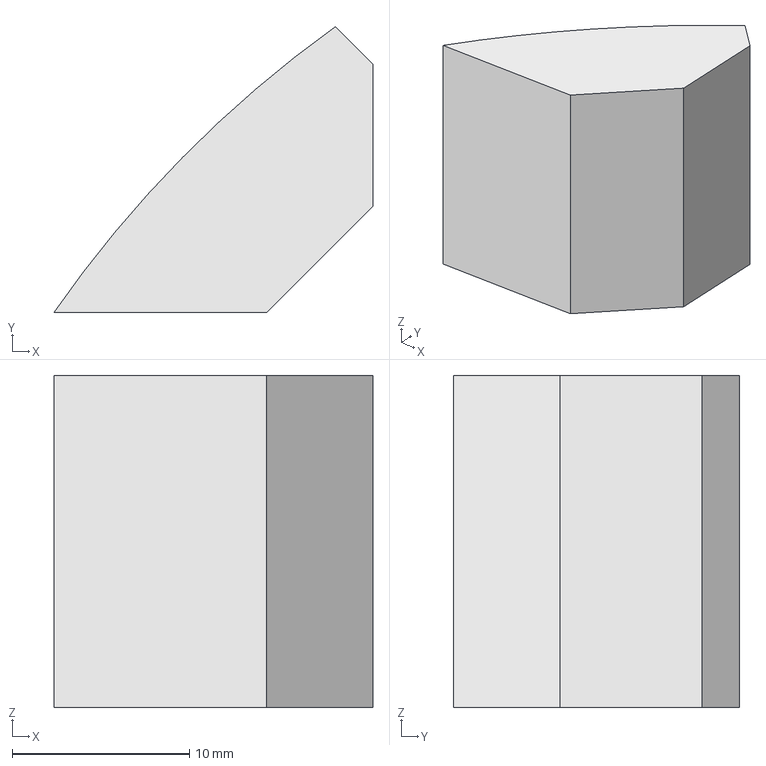
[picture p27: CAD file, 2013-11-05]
av4/avionics-rings/DBlock.step
18.0 x 16.1 x 18.8 mm

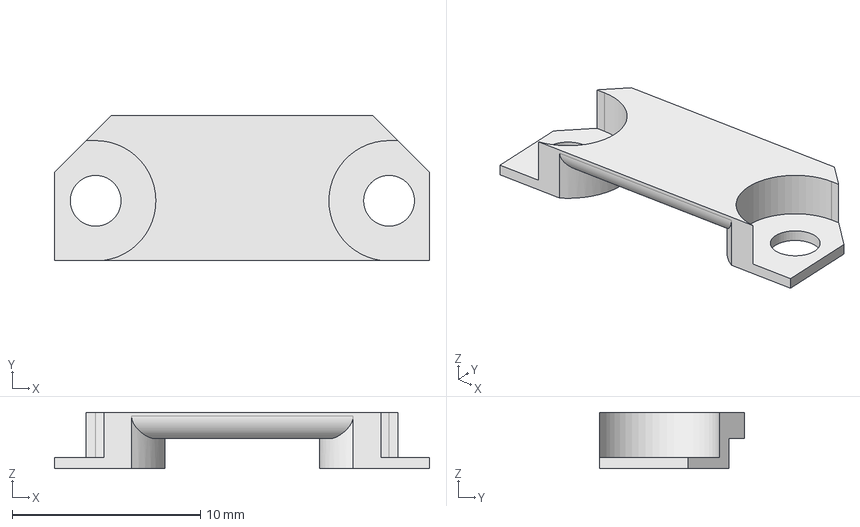
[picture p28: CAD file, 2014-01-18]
av4/rocketnet-connector/3d/parts/wire_head_RA.part.fcstd
19.9 x 7.70 x 3.00 mm

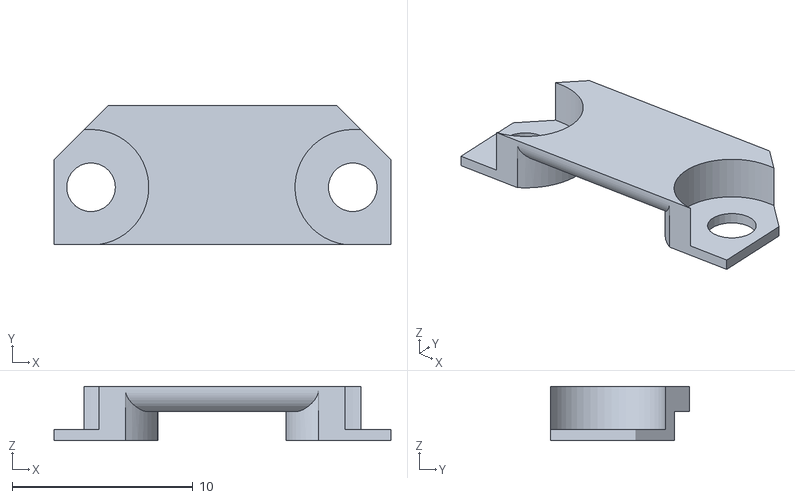
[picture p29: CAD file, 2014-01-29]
av4/rocketnet-connector/3d/print/top_RA_14.stl
18.7 x 7.70 x 3.00

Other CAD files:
av4/raspi-camera/datasheets/raspi.fcstd
av4/rocketnet-connector/3d/rocketnet-connector-14pin.assemb.fcstd
av3/rocketbus-connector/CAD/parts/Bottom_Bracket.part.fcstd
av4/avionics-rings/DBlock.part.fcstd
av3/rocketbus-connector/CAD/5mm_lock_nut.fcstd
av3/rocketbus-connector/CAD/5mm_lock_nut.stl
av3/rocketbus-connector/CAD/JED_connector_base.part.fcstd
av3/rocketbus-connector/CAD/JED_connector_top.part.fcstd
av3/rocketbus-connector/CAD/Standoff.part.fcstd
av3/rocketbus-connector/CAD/standoff_1.05.stl
av4/avionics-rings/RF-Channel.step
av4/avionics-rings/RF-channel.part.fcstd
av4/rocketnet-connector/3d/parts/Base_CircuitBoard.stp
av4/rocketnet-connector/3d/parts/Daughter_Board.part.fcstd
av4/rocketnet-connector/3d/parts/Daughter_Board.stp
av4/rocketnet-connector/3d/parts/bottom_bracket.part.fcstd
av4/rocketnet-connector/3d/parts/m50-3150642_asm.stp
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

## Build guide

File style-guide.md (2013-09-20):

# PSAS PCB CAD Style Guide

Here are some general suggestions for making schematics and PCB layouts for PSAS. Note that as of Fall 2013, we're using EAGLE CAD v6.5 as our standard CAD platform, so some of these suggestions may be "EAGLE-centric".

## Part Libraries

- We tend to put families of components in a single library. Name the library by the generic or root part number, if possible. This is crazy, we know, but we blame EAGLE.
- Normally we tend keep the libraries with the schematic we created them for. We should probably stop that.

## Schematics

### Schematics Symbols

- We like to use "American" symbols for R (triangle waves) and L (loop-de-loops) components, but "European" for C (parallel lines).
- ICs:
   - Do a "schematic symbol" rather than a "package symbol".
   - Power on the top, GND on the bottom, and generally inputs on the left, outputs on the right.
   - Don't be afraid to break up the IC into multiple symbols if it has a lot pins.
   - Sometimes it's nice to draw in details inside the chips, but not necessary.
- Make sure text doesn't overlap.
- Dont't forget to add a part number (>NAME) and value (>VALUE). We'll use the value for the exact part number.
- Be sure to set the "direction" of the pin correctly. Specifically, PWR, IN, OUT, and IO.

## Component packages

- All silkscreen marks for chips should be on the TPLACE layer and should not, in general, go over a pad.
- Use lines on the TDOC layer to complete marks for chips that would have gone over pads.
- Don't forget pin 1 num bers.
- Don't forget to put >NAME on the NAMES layer and >VALUE on the VALUES layer.

### Nets and Busses

- Name ALL important nets and MOST normal nets. Short little trivial nets don't need to be.
- Data and power flow left to right. Try to arrange the circuit that way.
- Power symbols are always vertical; positive symbols (VCC,5V,etc) point up and the net goes down, and negative symbols (GND, VSS, etc) point down and the net goes up.
- Supply symbols should be used for any power connection that has more than about 2 nodes.
- Use off-sheet style labels for all labels that go off sheet.
- Please use busses whenever 3 or more nets go in generally the same place.

### Part Numbers

- We have a whole spec for that: <http://psas.pdx.edu/RocketNames/>

### Misc

- PLEASE use Frames. Start with "B" size frames (11 x 17). It bounds the schematic, and also adds coordinates to cross reference connectors.
- Put the frame's origin on the sheet origin.
- On the INFO layer, put boxes and text labels describing the function of various component blocks.
- PUT DESCRIPTIVE INFORMATION IN THE SCHEMATIC (on the info layer)! Remember, the schematic should be "self documenting". What are the inputs? the outputs? Voltages? Currents? Description of what it does? Etc.

## Layout

## Power planes.

- Flood top and bottom layers with ground, except when it's not a good idea for RF or whatnot.
- On four layer boards, layer 2 is ground and layer 3 is power.
- Pull in the power layer by 3-4 mm from the edge of th board. Even better, ring it with ground if possible.
- Stich all multiple-layer ground planes. we like to do one <= 2 cm or so, and around the corners of the board.
- Do NOT interrupt layer 2 ground planes. Try not to interrupt layer 3 power planes.

## Traces and Vias

- Use the smallest possible round vias. That's usually a 0.254 mm (10 mil) drill or larger.
- Target 0.16/0.16 mm (6/6 mil) trace rules 
- Use the largest easily usable trace width. Go down to the design rules only when you have to.

## Component names

- Use the smallest possible component names: smash everything on the TNAME layer and switch to a text size of 0.8128 and a ratio of 20%.
- Place the component name as close as possible to the package. If you can't move it someplace obvious where it can't be mixed up with another part.
- If there's a tight layout, place the names in the same geometric layout as the components somewhere off to the side of the tight layout.

## Misc

- Put a name, version, and date on the silk layer, or copper layer if there's no silk.
- PSAS logos are a bonus.
- Switch all font to vector font.

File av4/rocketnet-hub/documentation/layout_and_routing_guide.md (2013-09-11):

# RocketNet Hub PCB Layout and Routing

## Guidelines

The PCB for this project must integrate multiple power domains, analog and digital signaling, and provide high reliability in a physically demanding environment. These consideration mandate that special care be taken while laying out the components and subsystems so that the external forces applied during flight pose only minimal threat to the board's operation. The KS8999 ethernet switch is a prime example of a component who's placement poses a significant risk to the board. It has large physical dimensions, high pin count (for a leaded chip), and has a large mass. The combination of size and mass could easily lead to cracked solder joints or lifted pads due to the high G forces experienced during lauch. Heat distribution of the battery charging circuit also poses a threat to board reliability. This document seeks to give the reader an understanding of the decisions made during layout and routing to meet the design goals. An understanding of basic layout guidelines is not required but will be beneficial to the reader.

The design is partitioned into four sub-systems:

1. Control system (microcontroller)
2. Communications (Ethernet)
3. Battery Charging
4. Off-Board interfaces

The design is also partioned into three power domains:

1. Battery/Shore power (4S LiPo battery pack = (10,14.7,16.8) V and shore power = (18,19,20)V which is called **+18V**
2. Digital Logic (+3.3V +/- 5%) called **+3v3**
3. Ethernet core (+2.1 V +/- 5%) called **+2v1**

The control system is the only subsystem that exists entirely within only one power domain, the digital logic domain. The remaining subsystems all interact with at least two domains. These relationships are listed here:

- Communications:
   - Digital Logic (Signaling only: MII and I2C interfaces)
   - Ethernet (KS8999 core and analog IO)
- Battery Charging:
   - Digital Logic (Signaling only: ACOK, I2C, and Current Mon)
   - Battery/Shore
- Off-Board Interfaces:
   - Battery/Shore (To nodes)
   - Digital Logic (Analog mux and signaling)

Placement of the subsystems should take into consideration the inter-domain dependencies listed above. Thus far we have physical mass, thermal dissipation, and power domain requirements to consider for placing the subsystems on the PCB. The final consideration that will impact the layout is accessibility of components that need to be accessed during testing, tuning, or final assembly. Once all of these considerations have been taken into account the layout of the subsystems becomes obvious to the most casual observer. Due to the signal density of the KS8999 it was determined that the communication system should be placed on one side of the board. The digital logic power domain interacts with all the other subsystems and thus it was placed in the center of the board. The battery charging system was placed on the other side of the PCB. 

## Component Placement

Component placement was determined using the following hierarchy of considerations:

1. Locality to other components as shown in the schematic
2. Indicators, IC's providing core functionality (or that have large physical size), test points, and tuning components go on top; everything else goes on the bottom.
3. Areas of high routing density should be avoided as much as possible.
4. Support components such as de-coupling caps, set resistors, and level shifting systems should be placed on the bottom level. (See item 2)

The guiding principle in laying out this board is that when looking at it mounted in the avionics section of the rocket the casual observer should assume that the board's functionality is simplistic and sized only to accomodate the required mounting holes. Granted, this is an example of designer vanity, but it nonetheless serves the purpose of showcasing the capstone team's unmatched skill at hardware design. :)

## Routing

There are three classifications of signals on this board: "high" speed (>=1MHz); low speed (<1MHz); and Power (>10mA). Nets in each of these classifications require different treatment when routing. High speed signals must be impedance controlled and length matched if differential. Power nets must be routed in a manner that accomodates the current requirements. Low speed nets are to be routed as if they were the poverty class of nets (wherever there is room and nobody objects too loudly). EMI generation is not a major concern as the device is only intended for operation in areas with few other electronic devices and even fewer people, however consideration will be made when routing high speed signals to conform to standard best practices for reducing EMI. All impedance controlled nets are to be routed over a continuous reference plane and are not to utilize mutiple layers. Power nets are to exist as planes or partial planes on internal layers. When a power net is to be connected to a device on an external layer, a polygon is to be created on that layer with minimum dimensions of 100 mil x 100 mil. Layer trasissions of power nets are to be accomplished through no less than four parallel vias (more should be used whenever possible to reduce paracitic inductance). Connections to a power net that serve only to pull a signal line high or low are exempted from the aformentioned requirements. A single via and connecting trace no less than 5 mil may be used when the pull is expected to consume > 1mA. Indicator LED's current limiting resistors are also exempt. A single via and connecting trace of at least 7 mil in width is acceptable for LED current limiting resistors. Low speed nets may be routed on any layer (though layer 14 and 15 are prefered) and may use up to 20 vias. External layers should not be used for routing of low speed or power nets for distances over 200 mil. Power nets should NOT be flood-filled on layers with highspeed nets routed on them--unless via stapling is used adjacent to all high speed routes. Vias to an interal power layer should be placed every (wavelength)/10 where the wavelegnth is calculated as the maximum analog wave setup on a high speed net at maximum switching frequency. This is to avoid the possibility of setting up resonant waves in the adjacent power fill areas that could rob the high speed nets of their power. For this particular PCB we have selected a 6 layer stackup with following layers:

1. Core components, indicators, high priority/high visibility signals
2. Power reference plane (GND)
3. Power (+18, +3.3, and +2.1V)
4. North/South routing (also known as layer 14)
5. East/West routing (also known as layer 15)
6. Support components and secondary routing layer (also known as layer 16)

## Design Rules

The board was designed specifically to meet Sunstone Circuits "Quickturn Q6/E6 service". An EAGLE CAD design rules file (.DRU) file can be found in the 'eagle' directory.

- 6 layer board
- Trace/Space: 5/5 mil
- Minimum drill: 8 mil
- Minimum via ring diam: 18 mil

## CAM and Manufacturing

An EAGLE CAD CAM job (.CAM) file can be found in the 'eagle' directory. Gerber files were created and sent directly to Sunstone, and then to Screaming Circuits for assembly guidelines.

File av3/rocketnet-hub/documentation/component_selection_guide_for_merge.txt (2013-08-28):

Component Selection Guide
---
This page aims to explain the reasoning behind the selection of each component used in the power and communications hub designed by the 2012-13 capstone team. The intention is to provide insight into the design decisions made however there is no intention to provide the reader with a comprehensive design example that is suitable for any purpose other than exact replication. The target audience is expected to have design experience with microelectronics power distribution and modern physical layer communications designs utilizing matched impedance differential signaling.

U1, MCU, ST Microelectronics STM32F407V100
---
For this project the MCU chosen was to not only to be used for our capstone design but also migrated to replace the MCU used on the Generic Front Ends (GFEs). Thus despite a push from the capstone team to use an Atmel AV32 or Atmel ARM MCU it was decided by PSAS that an ST Micro STM32F407 MCU would be used. This microcontroller does offer some cost advantages over Atmel's offerings both in per unit cost and the cost of development tools. Given that PSAS is a cost conscious group that has ample expertise to draw from, the higher quality documentation offered by Atmel did not justify the added expense. Several Olimex STM32-E407 development boards where acquired and used by the PSAS software team to concurrently develop firmware for the RocketNet-Hub.

* Support Components

 * Crystal (C106, C107, and X1 -- 8Y-25.000MEEQ-T)

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

 * Bypass Caps 

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

 * Analog Supply Filtering (E5)

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

* Interfaces

 * Reset Logic

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

 * JTAG (J22)

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

 * Serial UART (J10)

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

 * MII

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

 * I2C (J11, R15, R17)

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

 * Rocket\_RDY (Q1, U3)

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

* Debugging

 * RBG LED (LED37)

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

 * Serial UART (J10)

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

 * JTAG (J22)

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

 * BOOT SEL (J5, J12)

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

* System Monitoring

 * Current Draw (U14, U15)

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

* System Control

 * Ethernet Switch (C12, D1, Q8, Q9, R43, R65)

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

 * Node Power

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

 * Voltage Supplies (C12, D1, Q8, Q9, R43, R65, U6)

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

 * Bypass Caps

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

 * Reset Circuitry (D2, D3)

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

 * Signal LEDs (LED1, LED5, LED9, LED13, LED17, LED21, LED25, LED29, LED33)

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

### U7, U8, U9, U10, U11, U12, U13, Node Power Switches, TPS2420

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

* Hard Current Limit (IMAX) (R51, R66, R67, R68, R69, R70, R71)
 
 Set by node--Set resistor on top side of PCB
* Soft Current Limit (IFLT) (R121, R122, R123, R124, R125, R126, R127)

 Set by node--Set resistor on top side of PCB
* Soft Limit Timer (CT) (C95, C96, C97, C98, C99, C100, C101)

 Set by node--Set Capacitor on top side of PCB
* Reset Behavior

 Latch reset condition and wait for MCU to reset switch

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

### U14, U15, Analog Multiplexers, MAX4734

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

# POWER SUPPLY BLOCK (Schematic sheet 3)

### U5, LTM8023 (2A, 36V DC/DC Step-Down μModule Regulator)

The board is powered by a 4-cell LiPo battery pack. This works out to a nominal voltage of just under 15(V) under battery power and under charging conditions the nominal voltage is 18(V). These voltages are far too high to run modern logic on. Also the potential swing in voltage is too large. The MCU can run on 1.8(V)-3.3(V). The design was intended to run on 3.3(V) initially. This became slightly more complicated after the selection of the KS8999 Ethernet Switch as this chip requires a 2.1(V) core voltage. The LTM8023 uModule from Linear Technologies was selected for its high level of integration and low external part count. The LTM8023 is capable of sourcing up to 2(A) of regulated power with an efficiency of 80%+. As the KS8999 requires 1(A) just by itself the 2(A) 3.3(V) supply seemed reasonable to source its LDO and the remaining logic. The Micrel MIC37101 line of LDO's was selected to source power to the KS8999. The MIC37101-2.1YM is a fixed voltage LDO with a typical output rating 1.6(A). This is 
sufficient to drive the KS8999 with reasonable headroom to account for potential variation. All resistors chosen came from each manufacturer's datasheet (with the exception of the LED current limiting resistor R128). The external components for the LMT8023 were provided by the manufacturer datasheet. The capacitors chosen for the Micrel MIC37101 were the minimum value recommended in the datasheet necessary to ensure stability.

* LTM8023 Settings
 * Vout: 3.3(V)
 * Osc. Freq.: 650KHz
 * Sync. Freq.: 650KHz -- set by MCU pll
 * R\_T (R74) 49.9KOhm
 * R\_ADJ (R73) 154KOhm
 * C\_in (C103) 2.2uF (0805)
 * C\_out (C104) 22uF (1206)
 * PGOOD LED (LED22) APT1608CGCK (Green 0603 V\_f 2.1V I\_d 20mA)
 * LED Current Limiting Resistor (R128) 750 Ohm (1.6 mA)
 * EN: Tied to supply voltage, Always on

### U6, MIC37101 (1A Low-Voltage μCap LDO)

* MIC37101-2.1YM Settings
 * EN: Weakly pulled to logic 0, controlled by U1.ETH_EN
 * C\_in (C52) 47uF
 * C\_out (C84, C85) 4.7uF, 0.1uF

# BATTERY CHARGING BLOCK (Schematic sheet 6)

### U2, Battery Charger, BQ24725

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

### In-Rush Limiter (R11, C60)

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

### Transient Voltage Suppression (D5)

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

### Enable (EN) Circuitry

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

### Various Capacitors

Sizes determined by component availability of 40V caps: >10uF 1206; =2.2uF 0805; >1uF(<2.2uF) 0603; <1uF 0402

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

### Negative Output (BAT) Voltage Protection (R144, R143)

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

### Inductor (L1)

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

### Input (C39, C43) and Output (C119, C120) Capacitors

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

### Power MOSFETs (Q2, Q3, Q5)

Power MOSFETs Selection (Q2, Q3 and Q5) detailed calculations on page 28 of datasheet.

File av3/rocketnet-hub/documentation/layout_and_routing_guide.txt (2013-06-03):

The PCB for this project must integrate multiple power domains, analog and digital signaling, and provide high reliability in a physically demanding environment. These consideration mandate that special care be taken while laying out the components and subsystems so that the external forces applied during flight pose only minimal threat to the board's operation. The KS8999 ethernet switch is a prime example of a component who's placement poses a significant risk to the board. It has large physical dimensions, high pin count (for a leaded chip), and has a large mass. The combination of size and mass could easily lead to cracked solder joints or lifted pads due to the high G forces experienced during lauch. Heat distribution of the battery charging circuit also poses a threat to board reliability. This document seeks to give the reader an understanding of the decisions made during layout and routing to meet the design goals. An understanding of basic layout guidelines is not required but will be beneficial to the reader.

Sub-system placement:
	The design can be partitioned into four sub-systems to assist in laying out the circuit. These are:
		1. Control system
		2. Communications
		3. Battery Charging
		4. Off-Board interfaces
	In addition to the four subsystems listed above the design is also partioned into three power domains. These are:
		1. Battery/Shore (+10 V to +18 V)
		2. Digital Logic (+3.2 V to +3.4 V)
		3. Ethernet (+2 V to 2.2 V)
	The control system is the only subsystem that exists entirely within only one power domain, the digital logic domain. The remaining subsystems all interact with at least two domains. These relationships are listed here:
		Communications:
			* Digital Logic (Signaling only: MII and I2C interfaces)
			* Ethernet (KS8999 core and analog IO)
		Battery Charging:
			* Digital Logic (Signaling only: ACOK, I2C, and Current Mon)
			* Battery/Shore
		Off-Board Interfaces:
			* Battery/Shore (To nodes)
			* Digital Logic (Analog mux and signaling)
Placement of the subsystems should take into consideration the inter-domain dependencies listed above. Thus far we have physical mass, thermal dissipation, and power domain requirements to consider for placing the subsystems on the PCB. The final consideration that will impact the layout is accessibility of components that need to be accessed during testing, tuning, or final assembly. Once all of these considerations have been taken into account the layout of the subsystems becomes obvious to the most casual observer. Due to the signal density of the KS8999 it was determined that the communication system should be placed on one side of the board. The digital logic power domain interacts with all the other subsystems and thus it was placed in the center of the board. The battery charging system was placed on the other side of the PCB. 

Components:
Component placement was determined using the following hierarchy of considerations:
	1. Locality to other components as shown in the schematic
	2. Indicators, IC's providing core functionality, test points, and tuning components go on top; everything else goes on the bottom.
	3. Areas of high routing density should be avoided as much as possible.
	4. Support components such as de-coupling caps, set resistors, and level shifting systems should be placed on the bottom level. (See item 2)
The guiding principle in laying out this board is that when looking at it mounted in the avionics section of the rocket the casual observer should assume that the board's functionality is simplistic and sized only to accomodate the required mounting holes. Granted, this is an example of designer vanity, but it nonetheless serves the purpose of showcasing the capstone team's unmatched skill at hardware design. 

Routing:
There are three classifications of signals on this board: "high" speed (>=1MHz); low speed (<1MHz); and Power (>10mA). Nets in each of these classifications require different treatment when routing. High speed signals must be impedance controlled and length matched if differential. Power nets must be routed in a manner that accomodates the current requirements. Low speed nets are to be routed as if they were the poverty class of nets (wherever there is room and nobody objects too loudly). EMI generation is not a major concern as the device is only intended for operation in areas with few other electronic devices and even fewer people, however consideration will be made when routing high speed signals to conform to standard best practices for reducing EMI. All impedance controlled nets are to be routed over a continuous reference plane and are not to utilize mutiple layers. Power nets are to exist as planes or partial planes on internal layers. When a power net is to be connected to a device on an external layer, a polygon is to be created on that layer with minimum dimensions of 100 mil x 100 mil. Layer trasissions of power nets are to be accomplished through no less than four parallel vias (more should be used whenever possible to reduce paracitic inductance). Connections to a power net that serve only to pull a signal line high or low are exempted from the aformentioned requirements. A single via and connecting trace no less than 5 mil may be used when the pull is expected to consume > 1mA. Indicator LED's current limiting resistors are also exempt. A single via and connecting trace of at least 7 mil in width is acceptable for LED current limiting resistors. Low speed nets may be routed on any layer (though layer 14 and 15 are prefered) and may use up to 20 vias. External layers should not be used for routing of low speed or power nets for distances over 200 mil. Power nets should NOT be flood-filled on layers with highspeed nets routed on them--unless via stapling is used adjacent to all high speed routes. Vias to an interal power layer should be placed every (wavelength)/10 where the wavelegnth is calculated as the maximum analog wave setup on a high speed net at maximum switching frequency. This is to avoid the possibility of setting up resonant waves in the adjacent power fill areas that could rob the high speed nets of their power. For this particular PCB we have selected a 6 layer stackup with following layers:
	1. Core components and indicators
	2. Reference
	3. Power (+18 and +3.3)
	4. North/South routing (also known as layer 14)
	5. East/West routing (also known as layer 15)
	6. Support components and secondary routing layer (also known as layer 16)
Physical dimensions to be used in manufacturing are as follows:
	* Spacing: 		 5 mil
	* Trace width:		 5 mil
	* min dril:		 8 mil
	* via ring diam:	18 mil

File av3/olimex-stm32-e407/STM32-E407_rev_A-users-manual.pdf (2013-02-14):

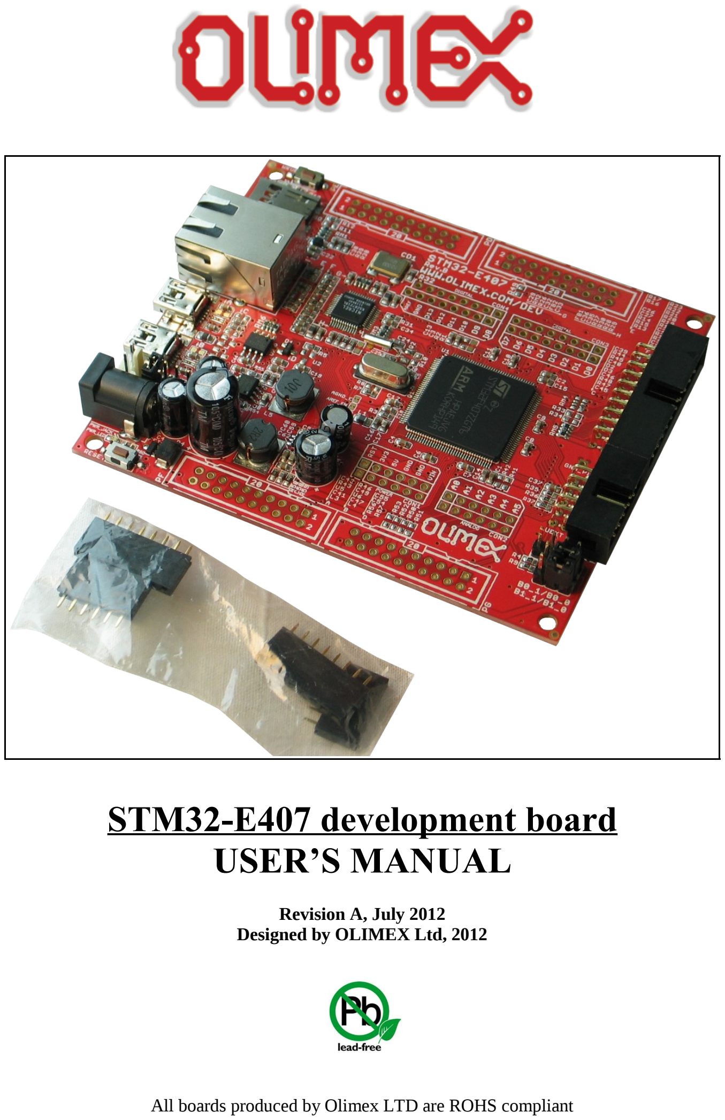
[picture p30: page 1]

# STM32-E407 development board USER’S MANUAL

Revision A, July 2012
Designed by OLIMEX Ltd, 2012

All boards produced by Olimex LTD are ROHS compliant

OLIMEX© 2012 | STM32-E407 User's Manual

### DISCLAIMER

© 2012 Olimex Ltd. Olimex®, logo and combinations thereof, are registered trademarks of Olimex Ltd. Other product names may be trademarks of others and the rights belong to their respective owners.

The information in this document is provided in connection with Olimex products. No license, express or implied or otherwise, to any intellectual property right is granted by this document or in connection with the sale of Olimex products.

The Hardware project is released under the Creative Commons Attribution-Share Alike 3.0 United States License. You may reproduce it for both your own personal use, and for commertial use. You will have to provide a link to the original creator of the project http://www.olimex.com on any documentation or website. You may also modify the files, but you must then release them as well under the same terms. Credit can be attributed through a link to the creator website: http://www.olimex.com

The software is released under GPL.

It is possible that the pictures in this manual differ from the latest revision of the board.

The product described in this document is subject to continuous development and improvements. All particulars of the product and its use contained in this document are given by OLIMEX in good faith. However all warranties implied or expressed including but not limited to implied warranties of merchantability or fitness for purpose are excluded. This document is intended only to assist the reader in the use of the product. OLIMEX Ltd. shall not be liable for any loss or damage arising from the use of any information in this document or any error or omission in such information or any incorrect use of the product.

This evaluation board/kit is intended for use for engineering development, demonstration, or evaluation purposes only and is not considered by OLIMEX to be a finished end-product fit for general consumer use. Persons handling the product must have electronics training and observe good engineering practice standards. As such, the goods being provided are not intended to be complete in terms of required design-, marketing-, and/or manufacturing-related protective considerations, including product safety and environmental measures typically found in end products that incorporate such semiconductor components or circuit boards.

Olimex currently deals with a variety of customers for products, and therefore our arrangement with the user is not exclusive. Olimex assumes no liability for applications assistance, customer product design, software performance, or infringement of patents or services described herein.

THERE IS NO WARRANTY FOR THE DESIGN MATERIALS AND THE COMPONENTS USED TO CREATE STM32-E407. THEY ARE CONSIDERED SUITABLE ONLY FOR STM32-E407.

## Table of Contents

### CHAPTER 1 OVERVIEW

### 1. Introduction to the chapter

Thank you for choosing the STM32-E407 single board computer from Olimex! This document provides a user’s guide for the Olimex STM32-E407 board. As an overview, this chapter gives the scope of this document and lists the board’s features. The differences between the members of the STM32-E407 and STM32-H407 boards are mentioned. The document’s organization is then detailed.
The STM32-E407 development board enables code development of applications running on the microcontroller STM32F407ZGT6, manufactured by STMicrocontrollers.

### 1.1 Features

- STM32F407ZGT6 Cortex-M4 210DMIPS, 1MB Flash, 196KB RAM, 3×12-bit 2.4 MSPS A/D, 2×12-bit D/A converters, USB OTG HS and USB OTG HS, Ethernet, 14 timers, 3 SPI, 3 I2C, Ethernet, 2 CANs, 3 12 bit ADCs, 2 12 bit DACs, 114 GPIOs, Camera interface
- JTAG connector with ARM 2x10 pin layout for programming/debugging
- UEXT connector
- 2 x USB-OTG
- SD-card
- Input DCDC power supply which allows operation from 6-16VDC source
- Power and User LEDs
- Reset and User buttons
- Arduino shield platform with provided headers
- 4 full 20-pin Ports with the external memory bus for add-on modules
- PCB: FR-4, 1.5 mm (0,062"), soldermask, silkscreen component print
- Dimensions: 10x76 mm (4''x3.40")

### 1.2 H407 or E407?

The major difference between STM32-E407 and STM32-E407 is that the latter has built-in Ethernet (physical level transceiver Micrel - Micrel datasheet). (http://www.micrel.com/_PDF/Ethernet/datasheets/ks8721bl-sl.pdf) STM32-E407 also features an extra USB-OTG and a number of SMD jumpers on the bottom which help the user to control the multiplexing on some pins easier. STM32-E407 has 2 x USB-OTG both with a miniUSB interface. STM32-H407 has 1 x USB-OTG and 1 x USB-HOST with the On-The-Go interfaced by miniUSB and the HOST by USB type A connector.

If you need built-in Ethernet check the STM32-E407.

### 1.3 Target market and purpose of the board

STM32-E407 is a development board featuring a powerful ARM Cortex-M4F microcontroller with the most important peripherals, interfaces and connectors mounted and ready to use. The board can be powered by a number of different sources, can be programmed via two different interfaces, has a TON of GPIO pins available on a number of headers. The board's Arduino platform headers give another option for enthusiasts who wish to implement support for Arduino/Maple/Pinguino shields giving the board additional features altogether with the option to add Olimex extension modules on the OLIMEX UEXT.

All of the above options make the board quite versatile and suitable for numerous tasks and situations. The power of ARM and the creativity of OLIMEX come at the best price and the well-known quality.

Every ARM enthusiast would see STM32-E407 as an interesting bargain and quite capable board for its low price.

### 1.4 Organization

Each section in this document covers a separate topic, organized as follow: – Chapter 1 is an overview of the board usage and features
– Chapter 2 provides a guide for quickly setting up the board
– Chapter 3 contains the general board diagram and layout
– Chapter 4 describes the component that is the heart of the board: the STM32F207ZET6 microcontroller
– Chapter 5 is an explanation of the control circuitry associated with the microcontroller to reset. Also shows the clocks on the board
– Chapter 6 covers the connector pinout, peripherals and jumper description
– Chapter 7 shows the memory map
– Chapter 8 provides the schematics
– Chapter 9 contains the revision history, useful links and support information

### CHAPTER 2 SETTING UP THE STM32-E407 BOARD

### 2. Introduction to the chapter

This section helps you set up the STM32-E407 development board for the first time.
Please consider first the electrostatic warning to avoid damaging the board, then discover the hardware and software required to operate the board.

The procedure to power up the board is given, and a description of the default board behavior is detailed.

### 2.1 Electrostatic warning

STM32-E407 is shipped in a protective anti-static package. The board must not be exposed to high electrostatic potentials. A grounding strap or similar protective device should be worn when handling the board. Avoid touching the component pins or any other metallic element.

### 2.2 Requirements

In order to set up the STM32-E407 optimally, the following items are required:

- JTAG or SWD interface programmer/debugger – can power the board and gives the ability to program/debug the board – to choose the correct programmer be sure that you are aware what software tools you are going to use when programming STM32-E407, and that the programmer supports STM32F407 processor.

Additional components can be acquired in order to increase the functionality of the board:

- External power supply
- SD-card or USB-mini cable or extensive UEXT modules are recommended but not required
- 3.7V Battery
- MOD-XXXX boards for additional features on the UEXT (RTC, TC, GSM, MP3, RS-485 among others) – note that you will have to implement the software setup between the boards
- Arduino/Maple/Pinguino shields – every shield is hardware compatible with H407 but will not work out-of-the-box, software implementation should be considered

Some of the suggested items can be purchased by Olimex, for instance:

ARM-USB-TINY-H – high-speed OpenOCD ARM JTAG debugger
ARM-USB-OCD-H – high-speed OpenOCD ARM JTAG debugger with buffer protection USB-MINI-CABLE USB mini to USB-A cable - USB mini to USB-A cable BATTERY-LIPO1400MAH – lithium-polymer battery 1400mAh
SY0612E - power supply adapter 12V/0.5A for iMX233-STM32-E407

### 2.3 Powering the board

The board is powered in one of the following ways: 1) by PWR jack, 2)by JTAG/SWD programmer (3)by USB-OTG.

The PWR jack should be supplied from a 6V to 16V source with maximum current of 1A from the power jack. Without additional components and peripherals (no microSD card mounted, nothing connected to the USB, etc.) the typical consumption is 30mA @ 12V. For the European customers we sell an affordable power supply adapter 12V/0.5A - SY0612E.

It is worth mentioning that the board can NOT be powered by the battery connector. The battery connected keeps some of the processor's functions remain intact during power down but it provides insufficient power for the board to operate properly. For example the RTC doesn't loose the values when there is a battery connected.

### 2.4 Prebuilt software

Upon powering initially the board's red PWR LED and the green PWR LED should turn on.

### CHAPTER 3 STM32-E407 BOARD DESCRIPTION

### 3. Introduction to the chapter

Here you get acquainted with the main parts of the board. Note the names used on the board differ from the names used to describe them. For the actual names check the STM32-E407 board itself.

The board comes with a bag with 4 headers for the Arduino/Maple/Pinguino platform which were left unsoldered in case you don't wish to use those environments or you don't plan on using shields.

There is also a bag of 4 rubber pads which can be placed in the 4 corner holes of the board. That way the board will be safe from short-circuiting on the bottom if placed on low-resistance surface. The placement stability of the board will also increase.

### 3.1 Layout (top view)

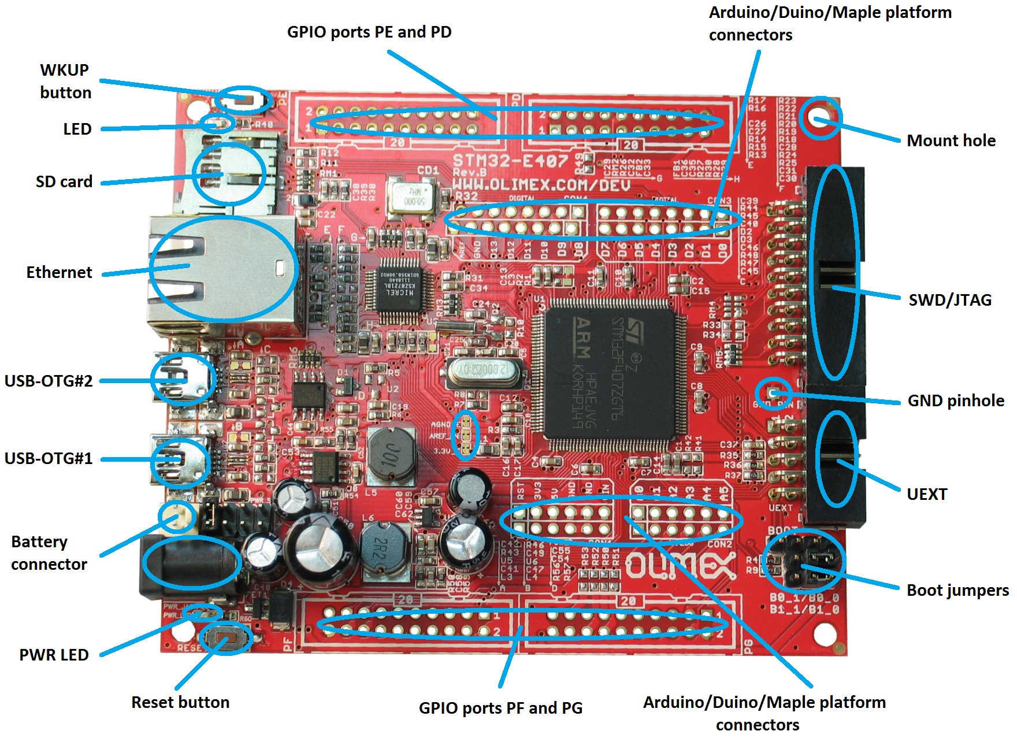
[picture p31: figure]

### 3.2 Layout (bottom view)

On the bottom there are three tables printed – general jumper table, boot mode jumper table, power mode jumper table. The default positions of the tables are also shown.

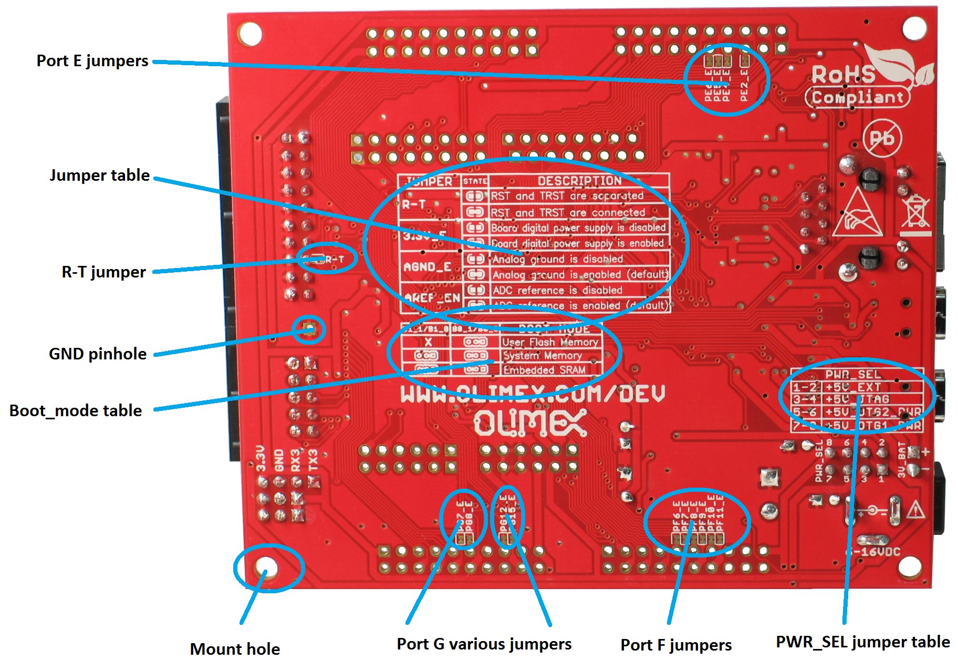
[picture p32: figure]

### CHAPTER 4 THE STM32F407ZGT6 MICROCONTROLLER

### 4. Introduction to the chapter

In this chapter is located the information about the heart of STM32-E407 – its Cortex-M4F microcontroller. The information is a modified version of the datasheet provided by its manufacturers from ST.

### 4.1 The STM32F407ZGT6 features

- Core: ARM 32-bit Cortex™-M4 CPU with FPU, Adaptive real-time accelerator (ART Accelerator™) allowing 0-wait state execution from Flash memory, frequency up to 168 MHz, memory protection unit, 210 DMIPS/1.25 DMIPS/MHz (Dhrystone 2.1), and DSP instructions
- Memories
- 1 Mbyte of Flash memory
- 192+4 Kbytes of SRAM including 64-Kbyte of CCM (core coupled memory) data RAM
- Flexible static memory controller supporting Compact Flash, SRAM, PSRAM, NOR and NAND memories
- LCD parallel interface, 8080/6800 modes
- Clock, reset and supply management
- 1.8 V to 3.6 V application supply and I/Os
- POR, PDR, PVD and BOR
- 4-to-26 MHz crystal oscillator
- Internal 16 MHz factory-trimmed RC (1% accuracy)
- 32 kHz oscillator for RTC with calibration
- Internal 32 kHz RC with calibration
- Sleep, Stop and Standby modes
- VBATsupply for RTC, 20×32 bit backup registers + optional 4 KB backup SRAM
- 3×12-bit, 2.4 MSPS A/D converters: 24 channels and 7.2 MSPS in triple interleaved mode
- 2×12-bit D/A converters
- General-purpose DMA: 16-stream DMA controller with FIFOs and burst support
- Up to 17 timers: up to twelve 16-bit and two 32-bit timers up to 168 MHz, each with up to 4 IC/OC/PWM or pulse counter and quadrature (incremental) encoder input
- Debug mode
- Serial wire debug (SWD) & JTAG interfaces

- Cortex-M4 Embedded Trace Macrocell™
- 114 I/O ports with interrupt capability
- Up to 15 communication interfaces
- 3 × I2C interfaces (SMBus/PMBus)
- 4 USARTs/2 UARTs (10.5 Mbit/s, ISO 7816 interface, LIN, IrDA, modem control)
- 3 SPIs (37.5 Mbits/s), 2 with muxed full-duplex I2S to achieve audio class accuracy via internal audio PLL or external clock
- 2 × CAN interfaces (2.0B Active)
- SDIO interface
- Advanced connectivity
- USB 2.0 full-speed device/host/OTG controller with on-chip PHY
- USB 2.0 high-speed/full-speed device/host/OTG controller with dedicated DMA, on-chip full-speed PHY and ULPI
- 10/100 Ethernet MAC with dedicated DMA: supports IEEE 1588v2 hardware, MII/RMII
- 8- to 14-bit parallel camera interface up to 54 Mbytes/s
- True random number generator
- CRC calculation unit
- 96-bit unique ID
- RTC: subsecond accuracy, hardware calendar

For comprehensive information on the microcontroller visit the ST’s web page for a datasheet.

At the moment of writing the microcontroller datasheet can be found at the following link: http://www.st.com/internet/com/TECHNICAL_RESOURCES/TECHNICAL_LITERATURE/DATASHEET/DM00037051.pdf (http://www.st.com/internet/com/TECHNICAL_RESOURCES/TECHNICAL_LITERATURE/DATASHEET/DM00037051.pdf)

### CHAPTER 5 CONTROL CIRCUITY AND HARDWARE MODULES

### 5. Introduction to the chapter

Here you can find information about reset circuit and quartz crystals locations, the power supply circuit is discussed.

### 5.1 Reset

STM32-E407's reset circuit includes R5 (10KΩ), R6 (1 KΩ), C19 (100nF) and a RESET button.

### 5.2 Clocks

There are two quartz crystals available on the board:

12 MHz quartz crystal Q1 is connected to pins 23 and 24 of the CORTEX-M4F processor.

Quartz crystal Q2 is a 32 768Hz RTC (real-time clock) and is connected to pins 8 and 9.

### 5.3 Power supply circuit

The power supply circuit of STM32-E407 allows flexible input supply from 6V to 16V direct current. This means a wide range of power supplies, adapters, converters are applicable. The maximum amperage the board can draw is 1A.

Note that the Li-Po battery connector cannot be used to fully power the board. It's function is to give an option to save internal data if the board needs to be relocated. It will keep the RTC alive, for instance.

If you have successfully powered the board the red PWR LED will turn on. Note that it is possible to have the PWR LED on even if there isn't enough power for proper operation of the board and all the peripherals currently connected.

### CHAPTER 6 CONNECTORS AND PINOUT

### 6. Introduction to the chapter

In this chapter are presented the connectors that can be found on the board all together with their pinout and notes about them. Jumpers functions are described. Notes and info on specific peripherals are presented. Notes regarding the interfaces are given.

Note that slashed signals (xxxx/yyyy) in the tables below might mean either multiplexing between signals or port name correspondence on the processor.

### 6.1 JTAG/SWD debug

The board can be debugged from the 20-pin JTAG connector either by a JTAG or a SWD compatible debugger. Below is the table of the JTAG. This interface can be used with the Olimex's OpenOCD debuggers.

JTAG/SWD interface
Pin # | Signal Name | Pin # | Signal Name

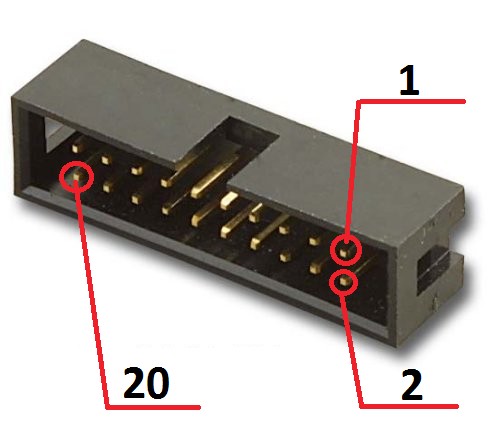
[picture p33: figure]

1 | +3.3V | 11 | -
2 | +3.3V | 12 | GND
3 | PB4/TRST | 13 | PB3/TDO
4 | GND | 14 | GND
5 | PA15/TDI | 15 | PB4/TRST
6 | GND | 16 | GND
7 | PA13/TMS | 17 | -
8 | GND | 18 | GND
9 | PA14/TCK | 19 | +5V_JTAG
10 | GND | 20 | GND

### 6.2 SD/MMC slot

The microSD card slot is a standard 8pin connector.

We have tested a number of microSD cards on the STM32-E407 boards and all of them worked fine regardless manufacturer or capacity. However, keep in mind that some of the lower quality microSD cards might draw too much current from the slot which might cause power-state problems. If you suspect the microSD card is causing problems please try using another one of better quality for better results.

microSD card connector
Pin # | Signal Name
1 DAT2/RES
2 CD/DAT3/CS
3 CMD/DI
4 VDD
5 SCL/SCLK
6 VSS
7 DAT0/RES
8 DAT1/RES

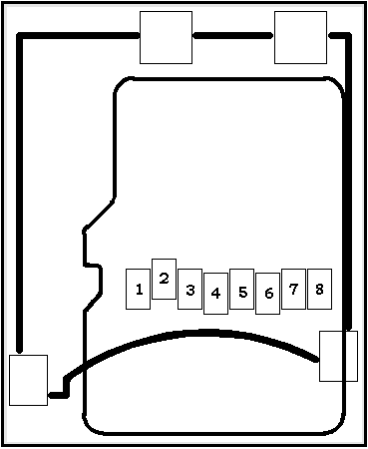
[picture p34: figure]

Notice that the pad numeration is written at the bottom of STM32-E407 under the microSD card connector.

When removing the card, please make sure that you release it from the connector by pushing and NOT by pulling the card directly (this can damage both the connector and the microSD card).

### 6.3 UEXT module

STM32-E407 board has UEXT connector and can interface Olimex's UEXT modules. For more information on UEXT please visit: http://www.olimex.com/dev/OTHER/UEXT.pdf

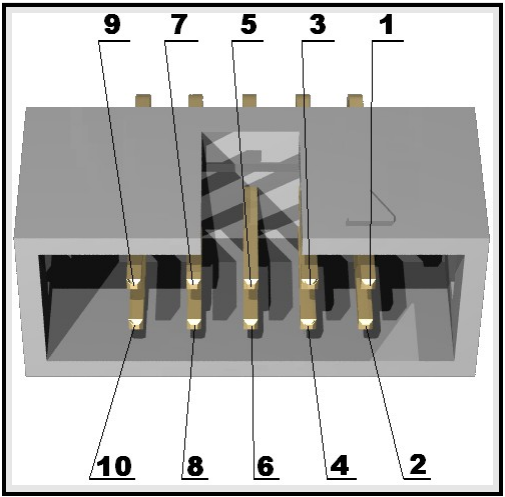
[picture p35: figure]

UEXT connector
Pin # | Signal Name
1 3.3V
2 GND
3 PC6/USART6_TX
4 PC7/USART6_RX

5 PB8/I2C1_SCL
6 PB9/I2C1_SDA
7 PC2/SPI2_MISO
8 PC3/SPI2_MOSI
9 PB10/SPI2_SCK/UART3_TX
10 PG10/UEXT_CS

### 6.4 USB_OTG1

USB On-The-Go, often abbreviated USB OTG, is a specification that allows USB devices such as digital audio players or mobile phonesto act as a host allowing a USB flash drive, mouse, or keyboard to be attached and also connecting USB peripherals directly for communication purposes among them.

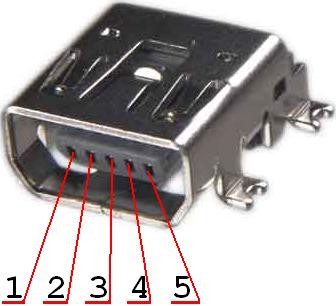
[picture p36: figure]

Pin # | Signal Name
1 +5V_OTG1_PWR
2 USB_OTG1_D-
3 USB_OTG1_D+
4 PA10/OTG1_FS_ID
5 GND

### 6.5 USB_OTG2

USB On-The-Go, often abbreviated USB OTG, is a specification that allows USB devices such as digital audio players or mobile phonesto act as a host allowing a USB flash drive, mouse, or keyboard to be attached and also connecting USB peripherals directly for communication purposes among them.

Pin # | Signal Name
1 +5V_OTG2_PWR
2 USB_OTG2_D-
3 USB_OTG2_D+
4 PB12/OTG2_HS_ID
5 GND

### 6.6 LAN connector

PIN# | SIGNAL NAME
1 TX+
2 TX-
3 VDD
4 NOT CONNECTED
5 NOT CONNECTED
6 NOT CONNECTED
7 RX+
8 RX-

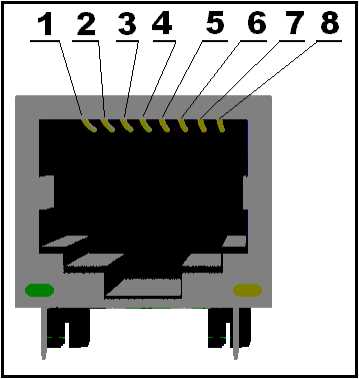
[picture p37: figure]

LED | Color | Usage
Right | Green | Link status
Left | Yellow | Activity status

### 6.7 Arduino/Maple platform

The Arduino/Maple platform connectors (2x6pin and 2x8pin plastic headers) are not mounted but are included in the package. The reasons for not mounting the headers on the pin holes are two: first you might not need them if you do not wish to experiment with Arduino/Maple software; second there are two rows depending on the shield you might want to use the difference between the two rows is the distance between the two digital rows one is made according to the Arduino shield standard (e.g. you want to mount the row there if using Arduino certified shield), the other one is adjusted properly at 100mil step (e.g. you want to solder the digital pins here if using properly adjusted shields).

The pinhole names are printed near the actual pinhole on the top of the board.

Arduino platform pinholes

CON1 | CON2
Pin | Signal Name | Processor pin# | Pin | Signal Name | Processor pin#
RST | RST | 25 | A0 | PC0 | 26
3V3 | 3.3V | - | A1 | PF6 | 18
5V | 5V | - | A2 | PF7 | 19
GND | GND | - | A3 | PF8 | 20
GND | GND | - | A4 | PF9 | 21
VIN | VIN | - | A5 | PF10 | 22

Arduino platform pinholes
CON3 | CON4
Pin | Signal Name | Processor pin# | Pin | Signal Name | Processor pin#
D0 | PB7/USART1_RX | 137 | D8 | PG12 | 35
D1 | PB6/USART1_TX | 136 | D9 | PG15 | 70
D2 | PE2 | 1 | D10 | PA4 | 40
D3 | PE4 | 3 | D11 | PB5 | 43
D4 | PE5 | 4 | D12 | PA5 | 42
D5 | PR6 | 5 | D13 | PA6 | 41
D6 | PG7 | 92 | GND | AGND | 31
D7 | PG8 | 93 | AREF | AREF | 32

6.8 20-pin connectors – PD – PE – PF - PG

The 4 20-pin connectors combine different processor ports and provide very nice GPIO option – you can use them with your breadboarding wires, you can mount headers, you can take measures, etc, etc.
Note that all 4 headers come without connectors (unlike the UEXT or the JTAG) and connectors are not included in the package (unlike the Arduino platform). However they follow the standard 100mil step connectors – not hard to find and mount/solder if needed etc.
PD | PE
Pin # | Signal Name | Pin # | Signal Name | Pin # | Signal Name | Pin # | Signal Name
1 | +3.3V | 11 | PD8 | 1 | +3.3V | 11 | PE8
2 | GND | 12 | PD9 | 2 | GND | 12 | PE9
3 | PD0 | 13 | PD10 | 3 | PE0 | 13 | PE10
4 | PD1 | 14 | PD11 | 4 | PE1 | 14 | PE11
5 | PD2/SD_MMC* | 15 | PD12 | 5 | PE2/D2* | 15 | PE12
6 | PD3 | 16 | PD13 | 6 | PE3 | 16 | PE13
7 | PD4 | 17 | PD14 | 7 | PE4/D3* | 17 | PE14
8 | PD5 | 18 | PD15 | 8 | PE5/D4* | 18 | PE15
9 | PD6 | 19 | +5V | 9 | PE6/D5* | 19 | +5V
10 | PD7 | 20 | GND | 10 | PE7 | 20 | GND
PF | PG
Pin # | Signal Name | Pin # | Signal Name | Pin # | Signal Name | Pin # | Signal Name
1 | +3.3V | 11 | PF8/A3* | 1 | +3.3V | 11 | PG8/D7*
2 | GND | 12 | PF9/A4* | 2 | GND | 12 | PG9
3 | PF0 | 13 | PF10/A5* | 3 | PG0 | 13 | PG10/UEXT_CS
4 | PF1 | 14 | PF11/A6* | 4 | PG1 | 14 | PG11/TX_EN
5 | PF2 | 15 | PF12 | 5 | PG2 | 15 | PG12/D8*
6 | PF3 | 16 | PF13 | 6 | PG3 | 16 | PG13/TXD0
7 | PF4 | 17 | PF14 | 7 | PG4 | 17 | PG14/TXD1
8 | PF5 | 18 | PF15 | 8 | PG5 | 18 | PG15/D9*
9 | PF6/A1* | 19 | +5V | 9 | PG6 | 19 | +5V
10 | PF7/A2* | 20 | GND | 10 | PG7/D6* | 20 | GND

Note that all signals marked with asterisk (*) are multiplexed with signals of the Arduino platform. Those signals can be controlled by the provided jumpers. However, the jumpers are soldered by default which enables them on the GPIO connector and the Arduino shield at the same time.

PG11, PG13, PG14, PG16 and PG17 are multiplexed with the UEXT and the Ethernet. Their connection is not controlled by jumpers.

### 6.9 PWR Jack

The power jack used is the typical 2.5mm one used by Olimex in most of our products. You should provide between 6 and 16 volts @ 1A to the board.

Pin # | Signal Name
1 Power Input
2 GND

More info about the power supply can be found in chapters 2 and 5 of this manual.

### 6.10 Battery connector

When using the battery connector keep in mind that it is an energy solution that wouldn't be able to power the board and all the peripherals!

It help keeping information in the processor if you need to transport the board from one power supply to other.

Pin # | Signal Name

1 VBAT
2 GND

The pin names are also written on the bottom of the board in the base of the connector.

### 6.11 U3BOOT

U3BOOT are 3 pinholes set on USART3 and are named on the bottom – GND, RX, TX3 and notice there are two vias near them which are actually VCC and can be used if connecting U3BOOT. More information about booting over UART can be found in the processor's datasheet.

### 6.12 Jumper description

Please note some of the jumpers on the board are SMD type. If you feel insecure in your soldering/cutting technique it is better not to try adjusting SMD jumpers.
Also if you feel incapable of removing the PTH jumper with hand better use tweezers. We do.

### 6.12.1 PWR_SEL

PWR_SEL is important PTH jumper allowing easy switching of input current. You can use tweezers to reach it. If you are powering the board via the PWR_JACK set it to position 1-2 (default → to the near edge of the board).

If powering from the JTAG/SWD set the jumper in position 3-4.

If powering from the USB-OTG2 set it in 5-6 position (near battery connector).

If powering from the USB-OTG1 set it in 7-8 position (near LAN connector).

The default position is 1-2.

### 6.12.2 B1_1/B1_0 and B0_1/B0_0

B1_1/B1_0 and B0_1/B0_0 are PTH jumpers which can be moved relatively easy.

Notice that these two jumpers must be moved together – they are responsible for the boot mode if bootloader is present. The board can search for bootloader on three places – User Flash Memory, System Memory or the Embedded SRAM.

If B0_0 is closed the board will try to boot from User Flash Memory.

If B0_1 is closed there are two variants depending on the state of B1_1/B1_0 jumper – if B0_1 is closed and B1_0 is closed the board will try to boot from System Memory. If B0_1 is closed and B1_1 is closed bootloader must be located in the Embedded SRAM.

The default positions are B0_0 and B1_0 (Boot from User Flash Memory).

### 6.12.3 R-T

This is SMD type jumper.

If you close/solder this jumper RST and TRST at the JTAG will be connected.

The default position is open/unsoldered.

6.12.4 3.3V_E
This is SMD type jumper.

Board digital power will be disabled if open/unsoldered

The default position is closed.

### 6.12.5 AGND_E

This is SMD type jumper.

If open/unsoldered will disable analog ground.

The default position is closed.

### 6.12.6 AREF_EN

This is SMD type jumper.

If open/unsoldered will disable ADC reference.

The default position is closed.

### 6.12.7 GPIO port jumpers

These are SMD type of jumpers located on the bottom of the board. They are located on the bottom of the board. We provided those in case you want to separate the multiplexing between the Arduino shield and the GPIO connectors. Check chapter 6.8 for more information on the multiplexing. Generally if you wish to avoid the multiplexing you have to cut the wire between the pads.

### 6.13 Additional hardware components

The components below are mounted on STM32-E407 but are not discussed above. They are listed here for completeness:

Reset button - used for hardware reset of the board

WKUP button – can be used as user button

User LED + Power LED

### CHAPTER 7 BLOCK DIAGRAM AND MEMORY

### 7. Introduction to the chapter

On the next page you can find a memory map for this family of processors. It is strongly recommended to refer to the original datasheet released by STMicroelectronics for one of higher quality.

### 7.1 Processor family block diagram

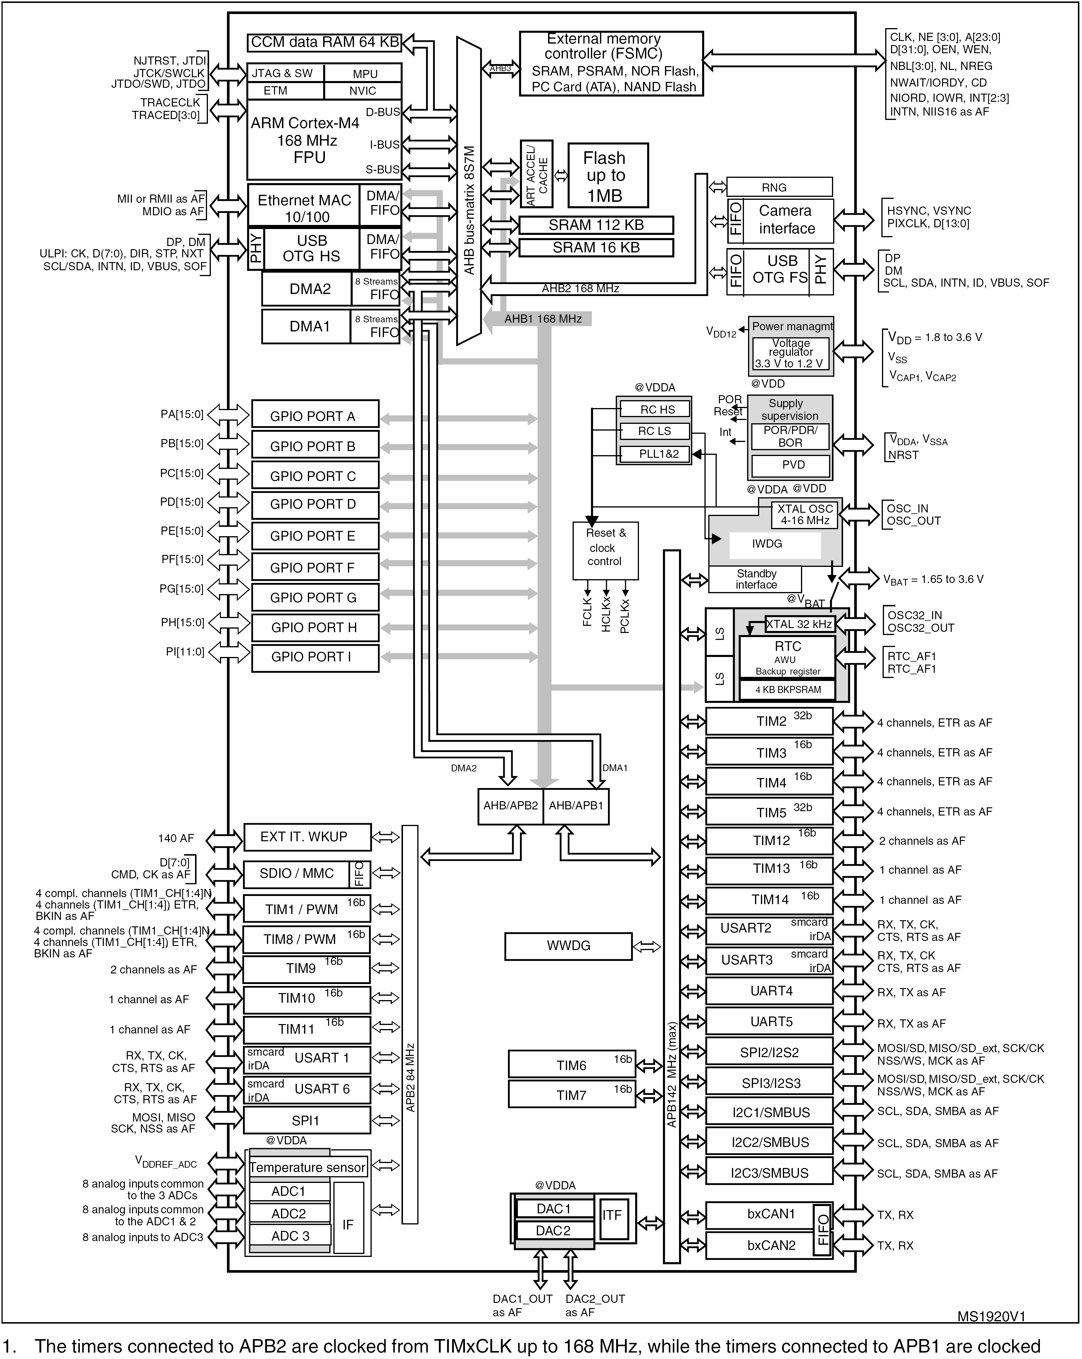
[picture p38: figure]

### 7.2 Physical memory map

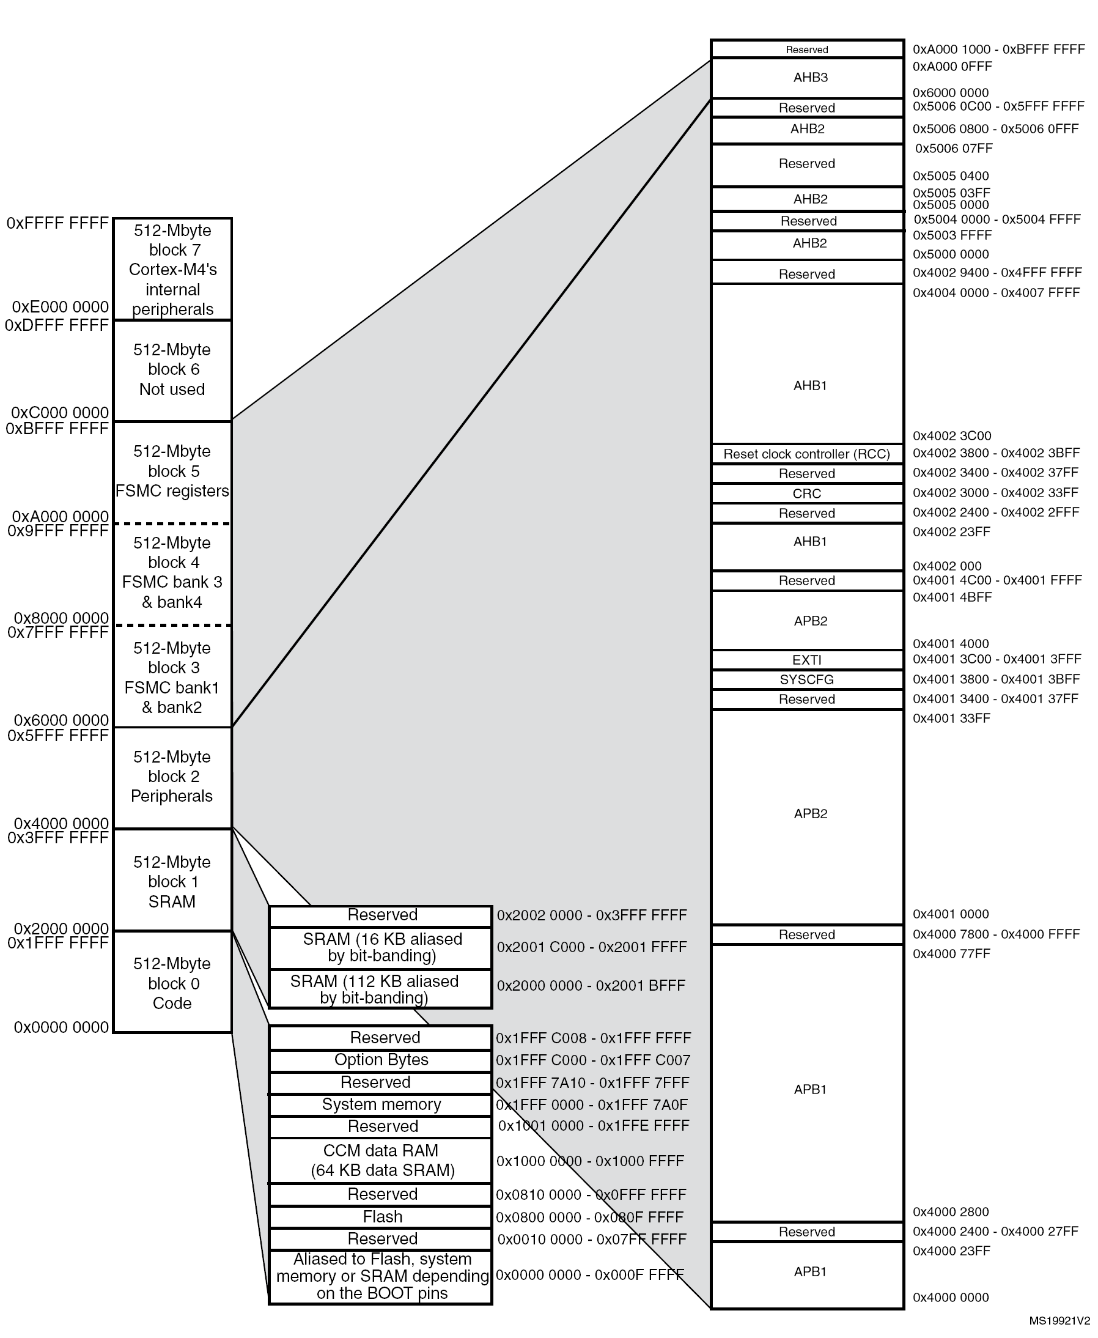
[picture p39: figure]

### CHAPTER 8 SCHEMATICS

### 8. Introduction to the chapter

In this chapter are located the schematics describing logically and physically STM32-E407.

### 8.1 Eagle schematic

STM32-E407 schematic is visible for reference here. You can also find them on the web page for STM32-E407 at our site: https://www.olimex.com/dev/STM32-E407.html. They are located in HARDWARE section.

The EAGLE schematic is situated on the next page for quicker reference.

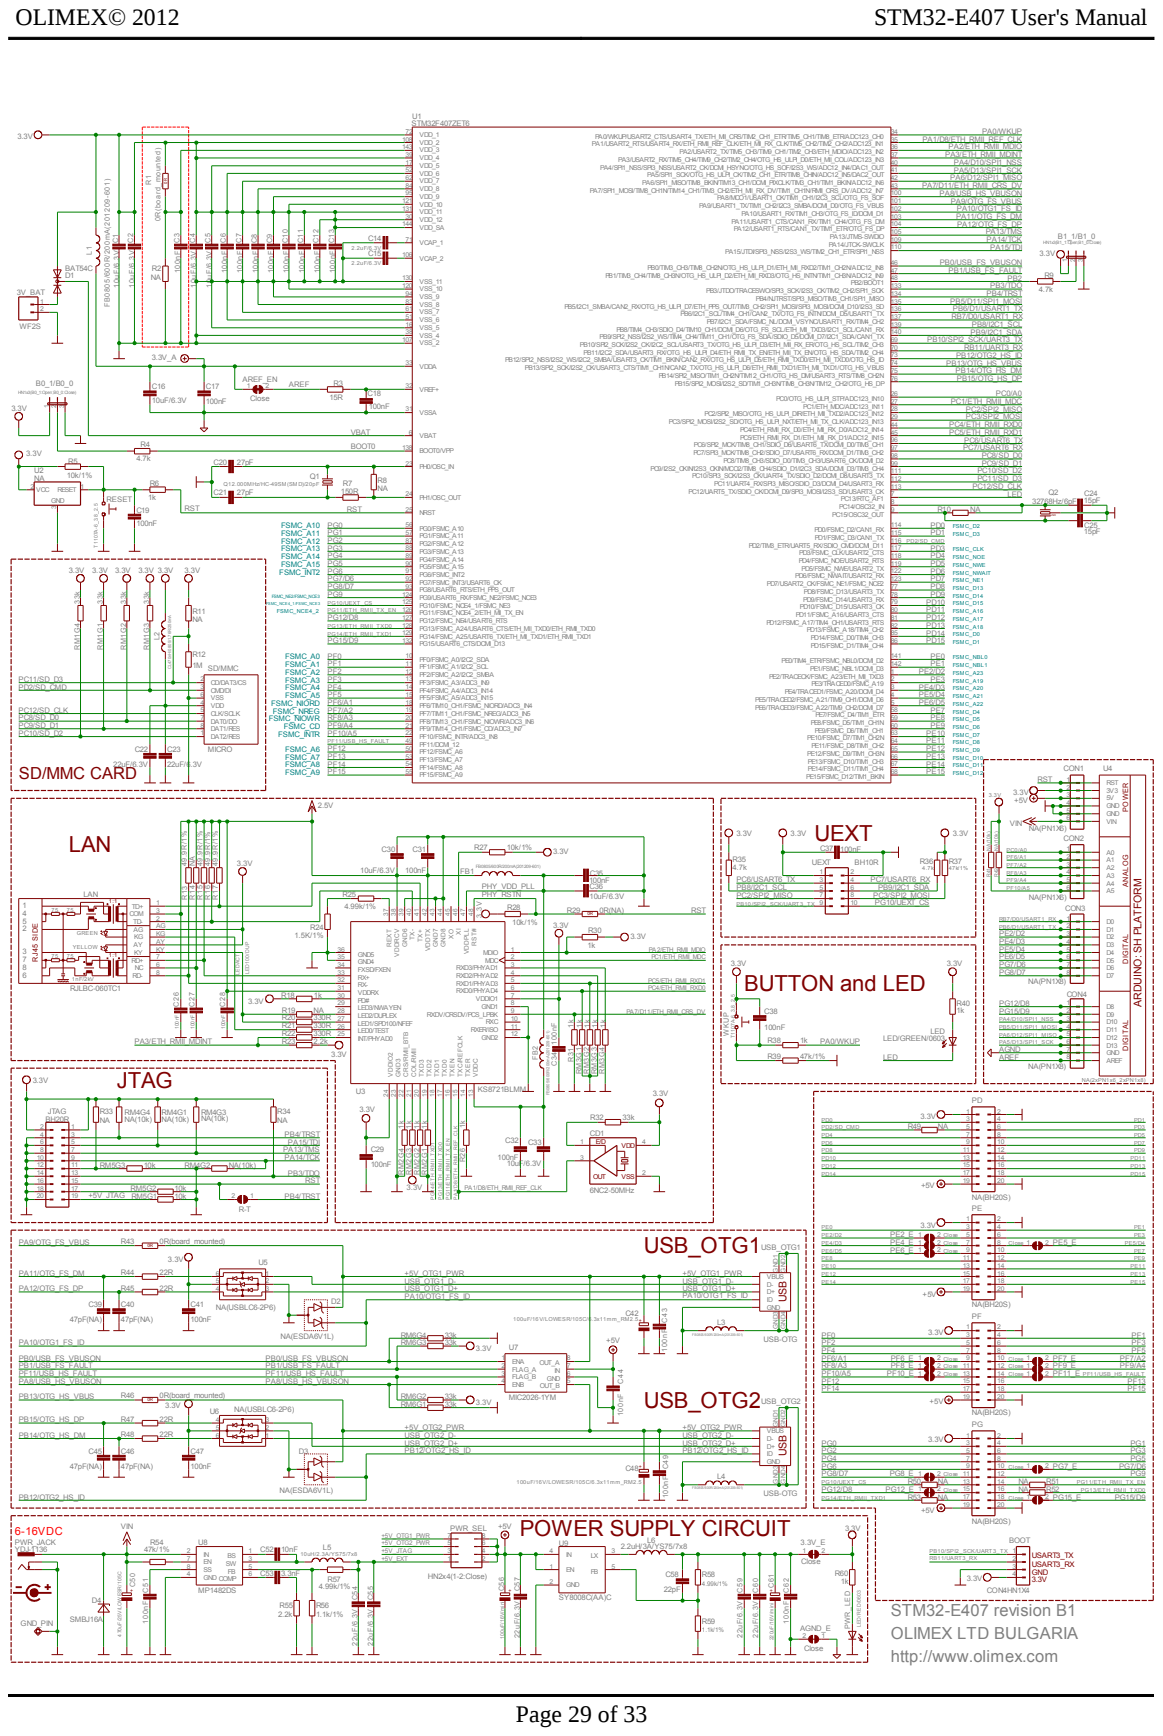
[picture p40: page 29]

PD2/SD_CMD | | PF4
PC12/SD_CLK | | PF5

CD/DAT3/CS 2 CMD/DI 3 VSS 6 VDD 4 CLK/SCLK 5 DAT0/DO 7 DAT1/RES 8 DAT2/RES 1 | PF3

PC8/SD_D0 | RF8/A3
PC9/SD_D1 | PF9/A4
PC10/SD_D2 | PF10/A5

POWER ANALOG DIGITAL DIGITAL

PB1/USB_FS_FAULT | Close 11 | 12 Close

LED/RED/0603
OLIMEX LTD BULGARIA
http://www.olimex.com

### 8.2 Physical dimensions

Note that all dimensions are in millimeters.

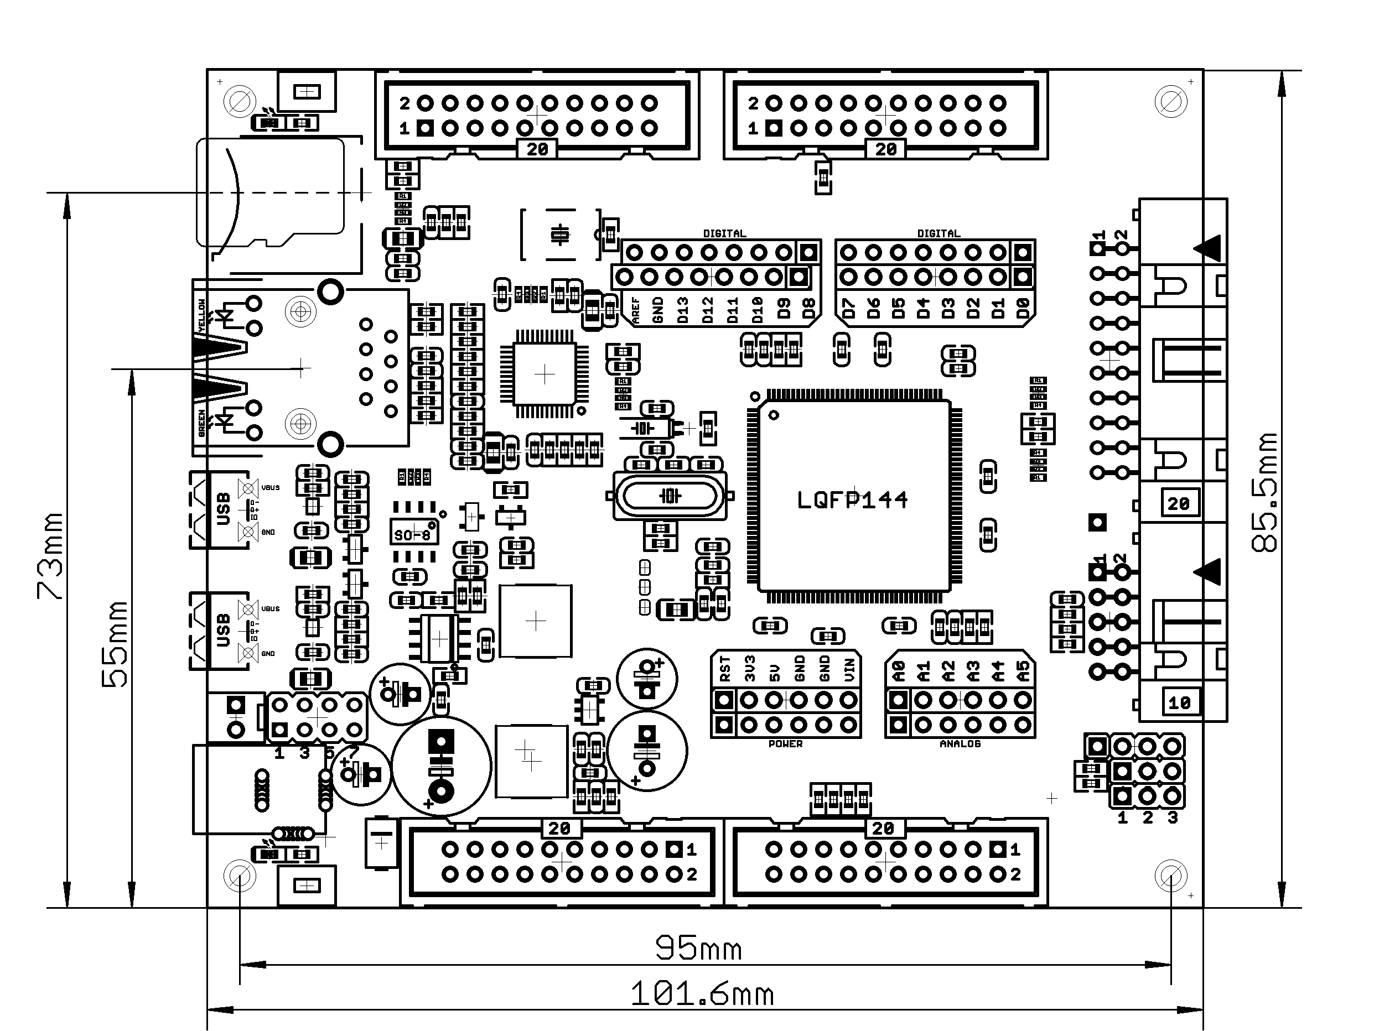
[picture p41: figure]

The three highest elements on the board in order from the tallest to the shortest are: capacitor C50 – 17.2mm (0.677'') over the pcb; LAN connector – 13.6mm (0.535''); capacitators C42 and C48 – 11.5mm (0.453'').

Note that the above measures does not include the PCB.

### CHAPTER 9 REVISION HISTORY AND SUPPORT

### 9. Introduction to the chapter

In this chapter you will find the current and the previous version of the document you are reading. Also the web-page for your device is listed. Be sure to check it after a purchase for the latest available updates and examples.

### 9.1 Document revision

Revision | Changes | Modified Page#
A, 25.07.12 | Initial Creation | All

### 9.1 Board's revision

Revision, Date | Revision Notes
B1, 07.06.12 | Initial release

### 9.3 Useful web links and purchase codes

The web page you can visit for more info on your device is https://www.olimex.com/dev/STM32-E407.html. (https://www.olimex.com/dev/stm32-h407.html)
You can get the latest updates on the software at: https://github.com/OLIMEX/STM32F4.

ORDER CODES:

STM32-E407 – the version of the board discussed in this document

STM32-H407 – the smaller version of the board without Ethernet

ARM-USB-TINY-H – OpenOCD compatible high-speed debugger/programmer with JTAG interface
ARM-USB-OCD-H – OpenOCD compatible debugger/programmer with JTAG interface, protection buffers and better power supply circuit
SY0612E - power supply adapter 12V/0.5A for STM32-E407 – 220V (European compatibility)

The latest price list can be found at http://olimex.com/dev/pricelist.html.

How to order?
You can order to us directly or by any of our distributors.
Check http://www.olimex.com/ and http://olimex.com/dev/order.html for more info.

### 9.3 Product support

For product support, hardware information and error reports mail to: support@olimex.com. Note that we are primarily a hardware company and our software support is limited.

Please consider reading the paragraph below about the warranty of Olimex products.

Warranty and returns:

Our boards have lifetime warranty against manufacturing defects and components.

During development work it is not unlikely that you can burn your programmer or development board. This is normal, we also do development work and we have damaged A LOT of programmers and boards during our daily job so we know how it works. If our board/programmer has worked fine then stopped, please check if you didn't apply over voltage by mistake, or shorted something in your target board where the programmer was connected etc. Sometimes boards might get damaged by ESD shock voltage or if you spill coffee on them during your work when they are powered.

Please note that warrany do not cover problems caused by unproper use, shorts, over-voltages, ESD shock etc.

If the board has warranty label it should be not broken. Broken labels void the warranty, same applies for boards modified by the customer, for instance soldering additional components or removing components - such boards will be not be a subject of our warranty.

If you are positive that the problem is due to manufacturing defect or component you can return the board back to us for inspection.

When we receive the board we will check and if the problem is caused due to our fault and we will repair/replace the faulty hardware free of charge, otherwise we can quote price of the repair.

Note that all shippings back and forth have to be covered by the customer. Before you ship anything back you need to ask for RMA. When you ship back please attach to it your shipping address, phone, e-mail, RMA# and brief description of the problem. All boards should be sent back in antistatic package and well packed to prevent damages during the transport.

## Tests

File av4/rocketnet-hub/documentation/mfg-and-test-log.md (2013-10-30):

# Notes on the manufacturing, bringup, and test of the Rocketnet Hub Boards

## LEFT TO DO

- Firmware all the things
   - 650KHz (?) clock for the LTM using TIMER1
- Look for noise on +3V3 and +2V1 supplies
- Done: Test battery charger on battery
- DONE: Create umbilical cord debugging cable (Shore power)
- DONE: Create rocketnet-to-ethernet cable with LED debugging cable
- DONE: Create battery debugging cable
- DONE: Create STM32 SWD cable
- DONE: Bring up STM32 and poke at GPIO things (port power switches, rocketnet, etc.)
- DONE: Get MII interface to work
- NA: Load KSZ8999 registers from STM32

## Summarized Issue List

- **Manufacturing/assembly Issues**
   - TODO: Populate "R21-17".
   - LED9 was reversed.
   - J22 should be an actual micro JTAG header with plastic shield.
   - Wrong RGB LED was purchased and installed.
   - LED9, LED5, LED1 were placed backwards.
   - Q1,Q9 (NTR4101) were not stuffed.
   - Added C52 except C52 is a 10uF 25V Y5V 
- **Design Issues that require modications to the board**
   - TODO: Remove R14 from board and schematic.
   - TODO: Connect VBAT to Vdd with a 100 nF bypass cap.
   - TODO: Replace U6 LDO with an SPS
   - TODO: Turn R18 into a divider to the system voltage for STM32 system voltage monitoring.
   - Grounded TP39 (`ETH_MII_RX_ER`) using mod wire.
   - Remove R10 on CFGMODE so the KSZ boots to its default settings
   - Port 8 !EN and !FLT are not connected to the STM32.   
- **Design Issues that require changes to component values**
   - TODO: R137 to 71.5 Kohm
   - TODO: C104 is spec'd as 22μF 1206 but is a 2.2 uF 0603.
- **Design Issues that should be fixed in the next design iteration (TODOs)**
   - Fix "R21-17" part number.
   - Add anti-aliasing filter to BQ24725 IOUT.
   - KSZ8999 link LEDs should be run off of 2.1V so they don't bleed 3.3V quiescent current into the KSZ.
   - Add EEPROM to an I2C bus so we can store critical state variables there.
   - BQ24725 VCC needs 10Ω + 1μF inrush limiter.
   - Give STM32 the ability to read the system battery and/or system voltage if BQ3060 board is not available.
   - PA8/MCO1 can't be used as the synchronization clock source, switch to a different pin.
   - J10 STM32 RX/TX should be reversed, and a different, shielded, more robust connector should be chosen.
   - This board should be brought up to the date with the node6 board; e.g., adding serial EEPROM off I2C for critical state info.

## 2013-09-27

- R14 isn't really necessary. In a flight environment, all nodes will be heard from within 300 s so internal aging of the source address (SA) doesn't matter.
- "R21-17" was not populated by SC. Probably because of the weird part number?

## 2013-09-22

- Firmware: PA8/MCO1 was putting a 15 MHz (?) clock into the LTM which was totally screwing it up and causing all sorts of terrible noise on the 3.3V line. We fixed that (made it GPIO, pulled it to ground) and everything works great, including SMBus communication to the BQ24725.

## 2013-09-22

- VBAT should be connected to Vdd with a 100 nF bypass cap (page 90 of reference manual).

## 2013-09-16

- Should change R137 to 71.5 Kohm to get a better ACOK range (see component selection notes)
- Probably add a anti-aliasing filter (active, or possibly passive), to IOUT.
- C104 is specified as 22μF 1206 in component selection notes but in the schematic is a 2.2 uF 0603.
- Just discovered U6, the 2.1 V LDO, is burning 1W of power at max KSZ load. OMFG. This needs to be replaced with a SPS. See component notes for more details, including possible replacement.
- It's pretty clear that the link light LEDs should be powered off of the 2.1 V supply, not the 3.3 V supply, to minimize quiescent current.
- On BQ24725, VCC needs an inrush limiter: according to datasheet, "Use 10Ω resistor and 1μF capacitor to ground as low pass filter to limit inrush current." Could this be the cause of some of the old APS BQ failures?
- There's no way for the RNH to read the battery voltage. While the BQ3060 will eventually be able to do this, it's stupid that the RNH can't do this. There turns out to be a very easy way to do this: Turn R18 current pulls down one of the MAX4734's CH1 input since it's otherwise a NC. Simply turn this into a divider to the system voltage. Don't use the battery voltage, since its farther away and not as protected.

## 2013-09-10

- STM32/KSZ MII interface now works!!11!!
   - ChibiOS was expecting a Micrel KSZ8721 PHY chip to talk to via the MII interface for packets *and* the MDIO (sometimes called MIIM, or more confusing, MII as in "management independent interface, because THAT'S not confusing :-/ ) interface for *link configuration*.
   - The KSZ8999 in "PHY" mode doesn't have an MDIO interface because there's really no PHY layer there, it's really just a raw MII interface.
   - Unsurprisingly, Chibios was built assuming a PHY chip with a MDIO interface, so we went down to the bottom level of the Chibios HAL (`mii_ldd.c`), down to the function that reads the registers from the MDIO interface (`mii_read`), and inserted a case statement that returned dummy "good" values for registers 0 (basic control), 1 (basic status), and 5 (100BASE-TX autonegotiation) of the KSZ8721 PHY chip. Basically we just guessed the "up and running with link" values, which shockingly just worked.

## 2013-09-03

- FIXED: LED9 was reversed.
- FIXED: grounded TP39 (`ETH_MII_RX_ER`) using green mod wire.
- All other link active LEDs seem OK
- We tested Ports 1-4, 6-8: link LEDs turn on.
- Built debug battery cable for providing power, and the first of the real rocketnet cables (rocketnet to RJ11).

## 2013-08-27 

Further Rocketnet-hub hacking

- DOH! We need a 25 MHz clock into the KSZ.
- PC9 is "microcontroller clock output 2" (MCO2), so we set it to output the HSE and no divisor and it just works.
- It works! It works! We get link lights and packets and even made the firmware commit using the rocketnet-hub!
- Next on the agenda: MII interface
- PA8 is MCO1 and goes to the LTM8023
   - Because MCO1 can only be 25 / 5 = 5 MHz, that's way too fast for the LTM. Make PA8 be `TMR1_CH1` and set that too... what?
   - Crystal lock frequncy needs to be looked at: initially, 650 + 20% KHz seems right be needs more investigation
   - Luckily, not critical, so we can skip this.

## 2013-08-20

Further bringup of board #1 with K and Gavin

- J10 STM32 RX/TX should be reversed on the UART connector, so that a reversed cable only grounds RX, not TX. Also, this connector is too small, and too fragile, to be used. It needs a shield, like the micro JTAG connector
- J22 should be an actual micro JTAG header with plastic shield, not just a pin header. Find part number and replace.
- FIXED: swapped out RGB LED for the right part number.
- Running the blinky light program, the RNH draws 13 mA.
- Put on the LED22 jumper, and it draws 14 mA.
- Got UART working; K has access to the ChibiOS shell!
- Holding `ETH_RST_N` low, we powered up the KSZ (brought `ETH_EN` high) and it draws 160 mA.
- Brought up `ETH_RST_N`, and RNH draws 150 mA (It went DOWN?)
- FIXED: Some link LEDs are not working: LED9, LED5, LED1. LED5 and LED1 look like they're placed backwards; LED9 looks OK though.
- FIXED: Removed R10 on CFGMODE in hopes that the KSZ would just boot to the default settings (CFGMODE has a "LPU" input which sets to 1 which should be EEPROM/not used, we think)
- Draws 130 mA now after flashing LEDs.
- Turned on all of the TPS power chips, they all turned on and all LEDs OK.
- Shorted out all node power with a 3 ohm resistor, all latched off and turned the red LEDs on.
- Toggling the `NODEn_EN_N` pins then turned the TPS back on!!
- RNH Ethernet to RNH Ethernet "just works"
- FIXED: RNH Ethernet to Switch or PC does not work.

## 2013-08-15

EEPROM research: It's not clear exactly what we need to do here. We initially thought we'd do the processor configuration, but there's no need to do anything besides bootstrapping, so we may not even need EEPROM control. Test: set SCL/SDA into floating inputs, and strap CFGMODE high and see if the KSZ just boots using its default settings. This will probably save us a lot of work, and means we don't have to be paranoid about loading the data on a KSZ reboot.

Conclusion: with CFGMODE floating, and no EEPROM, the KSZ eval board just works. Thus, we should remove R10 from the board and not bother to config the KSZ until we absolutely have to.

## 2013-08-14

Further bringup of board #1: with K, programming the STM32.

- Edited board.h to temporarily bring up the board safely (most things inputs that are pulled down).
   - Changed all the GPIO, HSE to 25 MHz and PLLM to 25.
   - Worked! Saw GPIO changing states at the right frequency.
- FIXED: The RGB LED we ordered was the wrong part number - pin layout of the LEDs is totally wrong. The PCB is designed for the LRTB G6TG-TU7+VV7+ST7-IB (DK 475-1319-1-ND) and what we specified in the BOM and thus stuffed is LTRBGFTM-ST7-1+VV9-29+Q5R (DK 475-2900-1-ND).
 
## 2013-07-28

Bring up of board #1.

- LED22 doesn't come on until about 5V
- Battery B+ @ 5V draws 11 mA. Bring it up to 7V and it draws 3 mA. +3v3 = 2.8 V
- Bring up to 10V, draws 3.7 mA and +3V3 = 3.361 V
- LED22 lights up with jumper in
- ISSUE: So does LED29 (Link light port #8). Because we pull down LED29 to GND using 1K and up to +3V3 using 750 ohm, it just turns on. Need a switch on the +3V3 line to the LEDs if we care.
- +2V1 = 75 mV
- Port 8 !EN is not connected to the STM32. It has an external ref designator `NODE8_!EN` but it doesn't go anywhere on the schematic.
- Pulling `NODE7_!EN` lights up LED16 and current jumps to 7.8 mA and `NODE7_VOUT` jumps from 35 mV to 10V.
- Checked all other `NODEn_!EN` and they turn on and off like NODE7.
- B+ @ 20V -> I=2.1 mA, +3V3 = 3.362 V
- UMB VIN = 5V draws 0.8 mA and nothing happens. Bringing VIN up to 18V starts flashing the over current LED and flashes LED22.
- The BQ24725 won't provide stop resetting until the 18V constant current is set to 900 mA. Then it turns on and draws 2.8 mA 
- On the Tek PS503A, turning on the power ALWAYS makes the power bounce once (LED 22 flashes once then turns on).
- BQ turns on power at VIN=18V, drops out again at 17.3V
- Added Q1,Q9 (NTR4101) 
- Added C52 except C52 is a 10uF 25V Y5V 
- Bringing `ETH_EN` up to 3.3V draws 218 mA from the B+=10V. At B+=16.8V, I = 137 mA
- +2V1 = 2.16V
- LED29 (PORT8 link) turns off immediately and LED38 (+2V1 power)
- 8 seconds later, all link LEDs blink twice then turn off
- FIXME-MFG: FIXED: LED9 did not turn on - it's reversed
- FIXME-NXT: all Link LEDs are slightly on (can't see in light, but in dark, you can see they're slightly on).
- POSSIBLE ISSUE: LED33 is on despite the fact the microcontroller has no code (is this right?)
 
## 2013-07-25

Received 4 stuffed boards and kit back from Screaming Circuits!

## 2013-07-22

Screaming circuit has issues with the kit:

- C52
    - Part Description: 4.7u, Capacitor, Ceramic,  X7R, 10%
    - Part Number: 445-14258-1-ND  Mfg Part Number: C1608X7S1A475K080AC
    - Issue: Forgot to order, weren't stuffed.
- L1
     - Part Description: 4.7 uH Low Profile, High Current IHLP
     - Part Number: 541-1010-1-ND  Mfg Part Number: IHLP-2525CZ-01
     - Issue: 4 were needed, got only 3, only 3 were stuffed.
- Q1,Q9
     - Part Description: MOSFET P-CH 20V 1.8A SOT-23
     - Part Number: NTR4101PT1GOSCT-ND  Mfg Part Number: NTR4101P
     - Issue: Forgot to deliver, weren't stuffed.

We told them to go ahead anyway, we'll stuff these parts by hand.

## 2013-06-17

Ordered boards! $1,460.30 for 4 boards (includes electrical test). That's $365 each.

## 2013-06-11

EAGLE board files handed off from 2012-2013 PSU ECE Capstone Team to PSAS.

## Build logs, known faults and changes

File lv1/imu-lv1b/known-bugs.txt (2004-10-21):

Known Bugs for LV1B imu-analog board v.1

imu main board trim cap does not connect to gyro amp A+ as it should
 ( 1 places, C402, backside)

Reference for ADXL202 circuit should be Vref, not Gnd.

Via got deleted for signal Theta Out on main board at daughter board connection

1uF cap does not clear PX sensor on backside, also 1uF cap seems spurious,
 why not throw in a 10uF? Whatever.

The 820uF inductor in the negative supply line creates a ground loop by raising
the analog board ground to ~0.45 Volts relative to the digital board. This can
be handled by removing the inductor, but shorting the ground planes doesn't
reduce the current consumption by more than 0.1mA, so removal may actually not
be warranted (but probably is). In future, however, i'd like to handle this
differently. The battery lines should be filtered, and the digital and analog
boards should have their true grounds heavily tied. This means circuits
switching the battery negative need to deal w/potentials below ground, but
though this is probably added complexity, it is required for reliability anyway.
Further, this arrangement should have significant noise advantages.

Daughter board signal ZO should not pass through on main board
(In fact all the daughter board connection on the main board should be checked
 and extended only to the traces they contact, and not to any perforating holes.)

Offset in J1 relative to flight computer (perhaps adjust FC?)
--Fixed by modifying FC

Added a 1nF feedfwd cap across voltage divider (maybe should be 1uF?)
Added boot-strap resistor from 5V to 6.025V supply (10k)
 Changed this resistor to a diode, which is both stiffer on start, making
 startup independent of load, and open after startup, saving power.
**********

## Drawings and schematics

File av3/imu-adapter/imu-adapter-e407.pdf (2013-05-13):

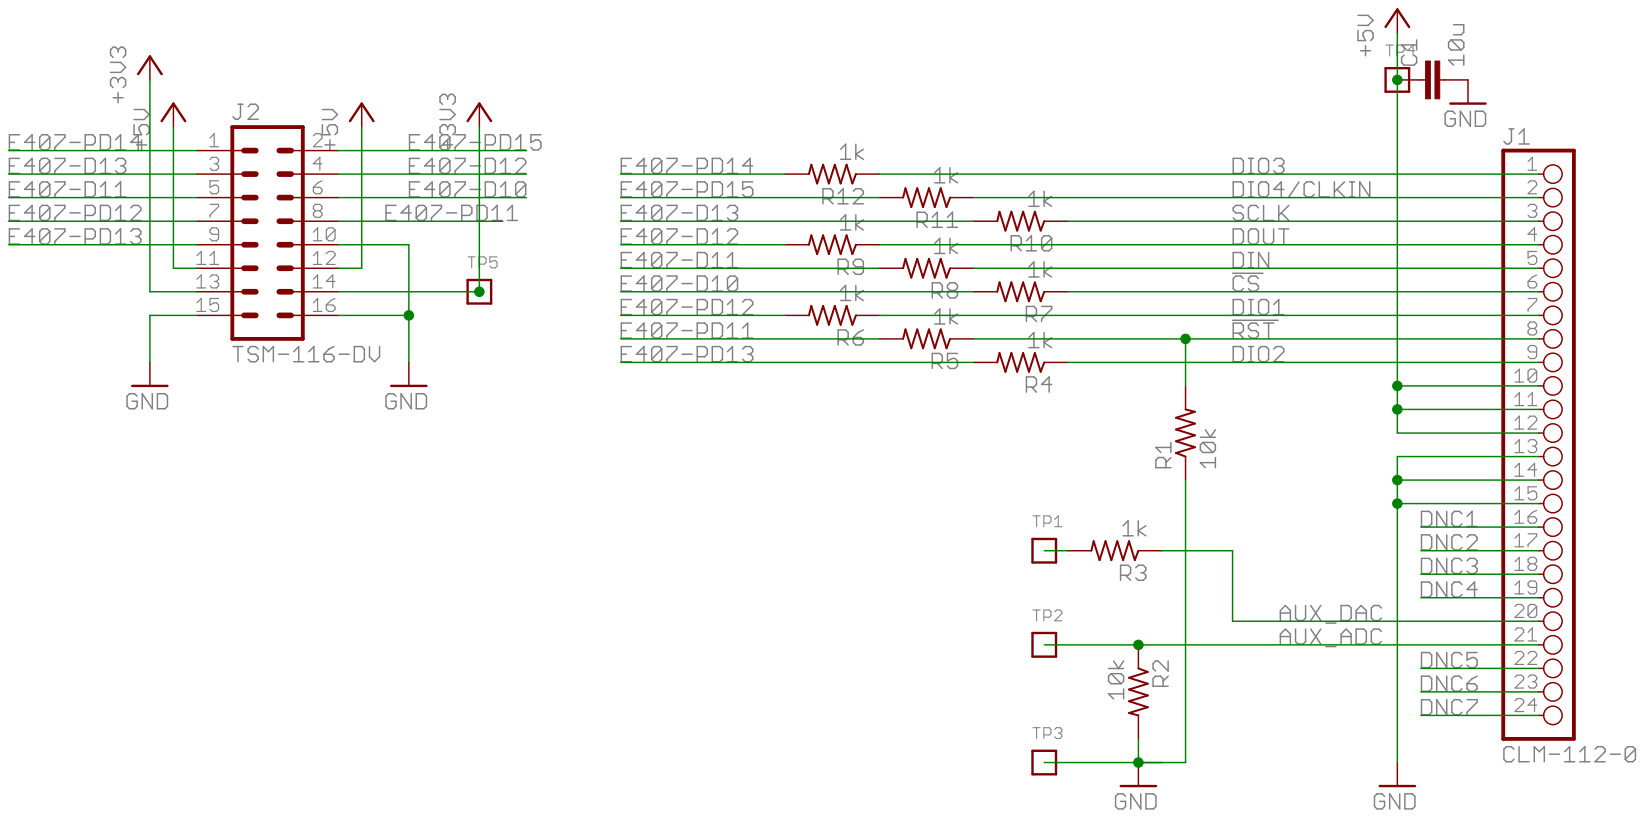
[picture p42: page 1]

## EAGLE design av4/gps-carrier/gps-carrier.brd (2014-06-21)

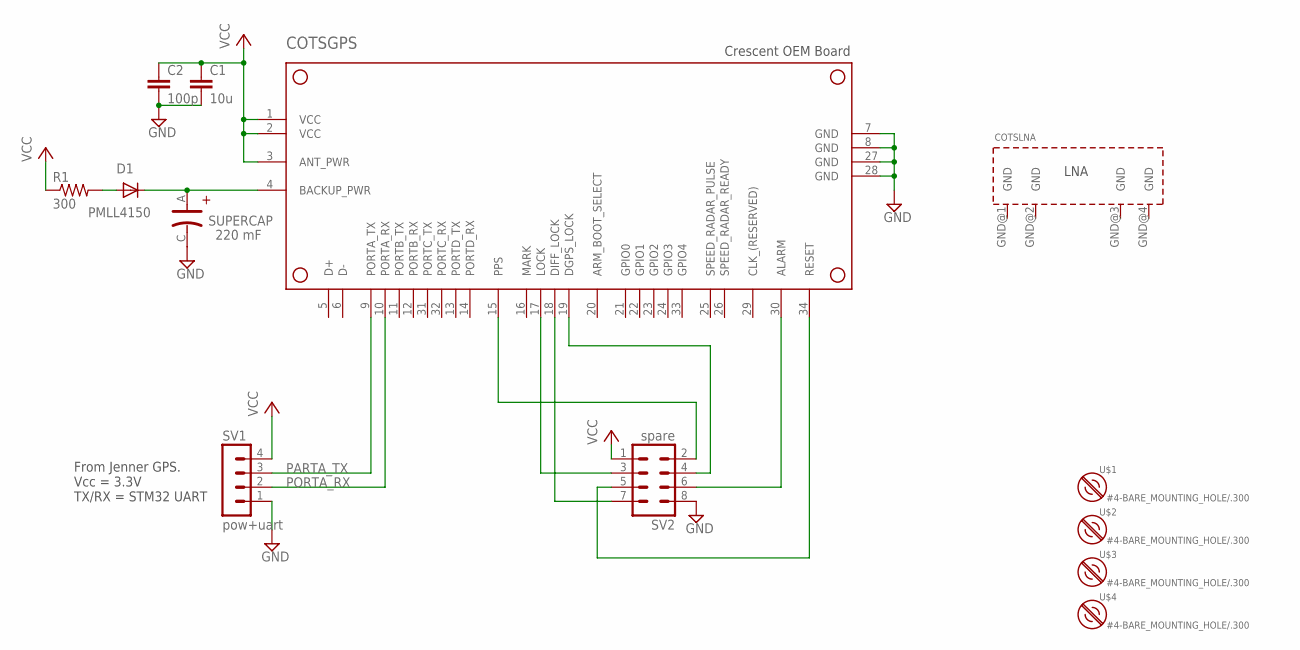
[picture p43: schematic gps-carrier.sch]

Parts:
C1: 10u; C0805
C2: 100p; C0603
COTSGPS: HEMISPHERE_GPS_MOUNT; GPS_CRECENT_OUTLINE
COTSLNA: GPS_LNA
D1: PMLL4150; SOD80C
R1: 300; R0603
SUPERCAP: 220 mF; DSK-HL
SV1: pow+uart; MA04-1
SV2: spare; MA04-2
U$1, U$2, U$3, U$4: #4-BARE_MOUNTING_HOLE/.300; #4/.300-BARE+STD_NUT_OR_STAR_WASHER

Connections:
ALARM: COTSGPS.30 (ALARM), SV2.6
BACKUPRAM: COTSGPS.4 (BACKUP_PWR), D1.C, SUPERCAP.A
DGPS: COTSGPS.19 (DGPS_LOCK), SV2.4
DIFF_LOCK: COTSGPS.18 (DIFF_LOCK), SV2.7
GND: C1.2, C2.2, COTSGPS.7 (GND), COTSGPS.8 (GND), COTSGPS.27 (GND), COTSGPS.28 (GND), SUPERCAP.C, SV1.1, SV2.8
LOCK: COTSGPS.17 (LOCK), SV2.3
unnamed: D1.A, R1.2
unnamed: COTSGPS.34 (RESET), SV2.5
PARTA_TX: COTSGPS.9 (PORTA_TX), SV1.3
PORTA_RX: COTSGPS.10 (PORTA_RX), SV1.2
PPS: COTSGPS.15 (PPS), SV2.2
VCC: C1.1, C2.1, COTSGPS.1 (VCC), COTSGPS.2 (VCC), COTSGPS.3 (ANT_PWR), R1.1, SV1.4, SV2.1

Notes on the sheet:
From Jenner GPS. Vcc = 3.3V TX/RX = STM32 UART

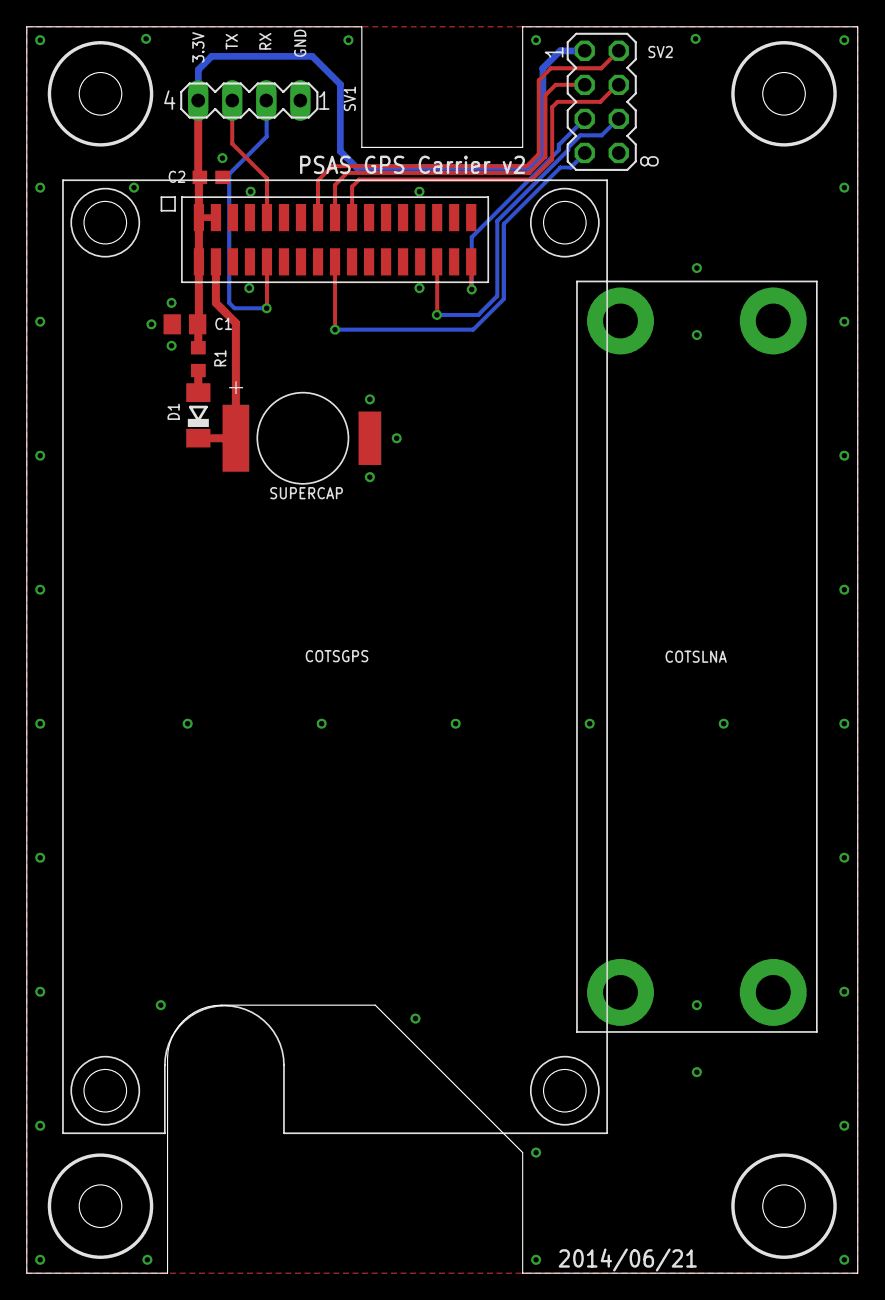
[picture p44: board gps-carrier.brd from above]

Board: 2 copper layers, 62.0 x 93.0 mm, 13 parts (0 on the bottom side), 12 nets.

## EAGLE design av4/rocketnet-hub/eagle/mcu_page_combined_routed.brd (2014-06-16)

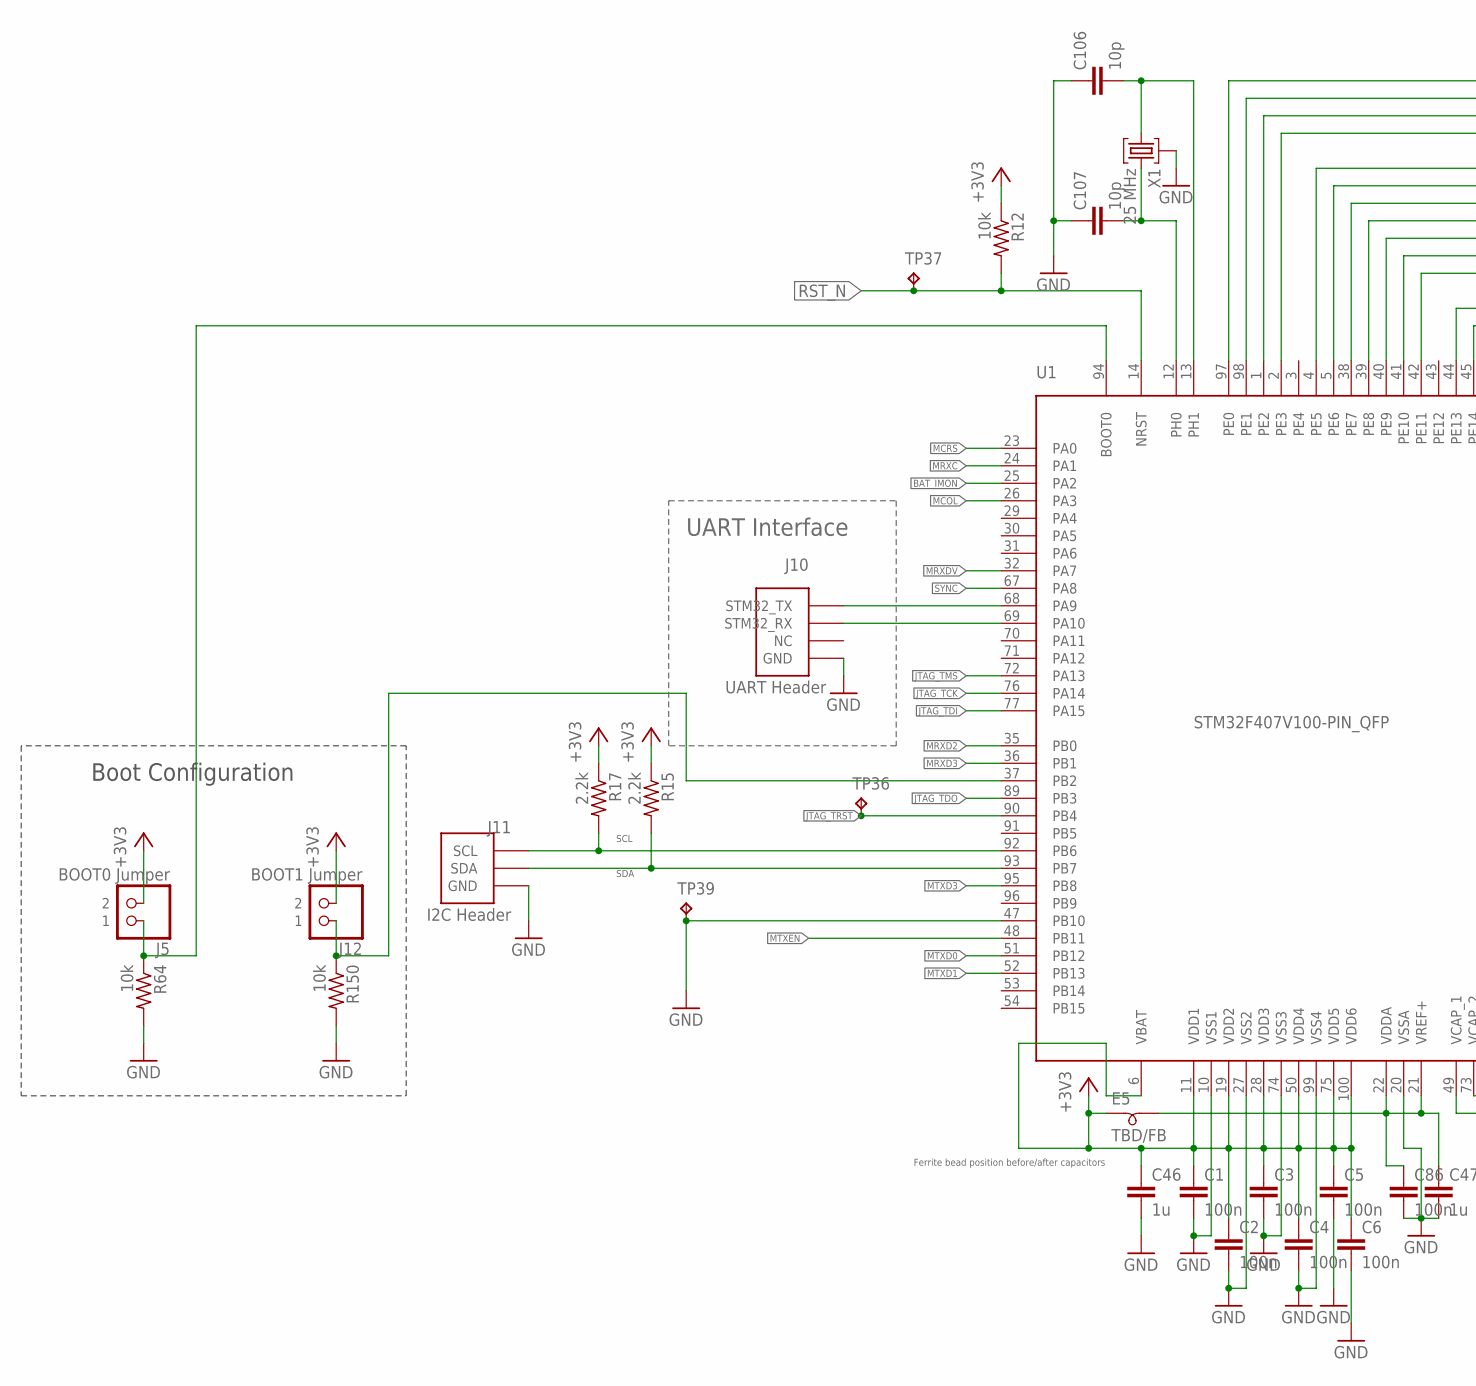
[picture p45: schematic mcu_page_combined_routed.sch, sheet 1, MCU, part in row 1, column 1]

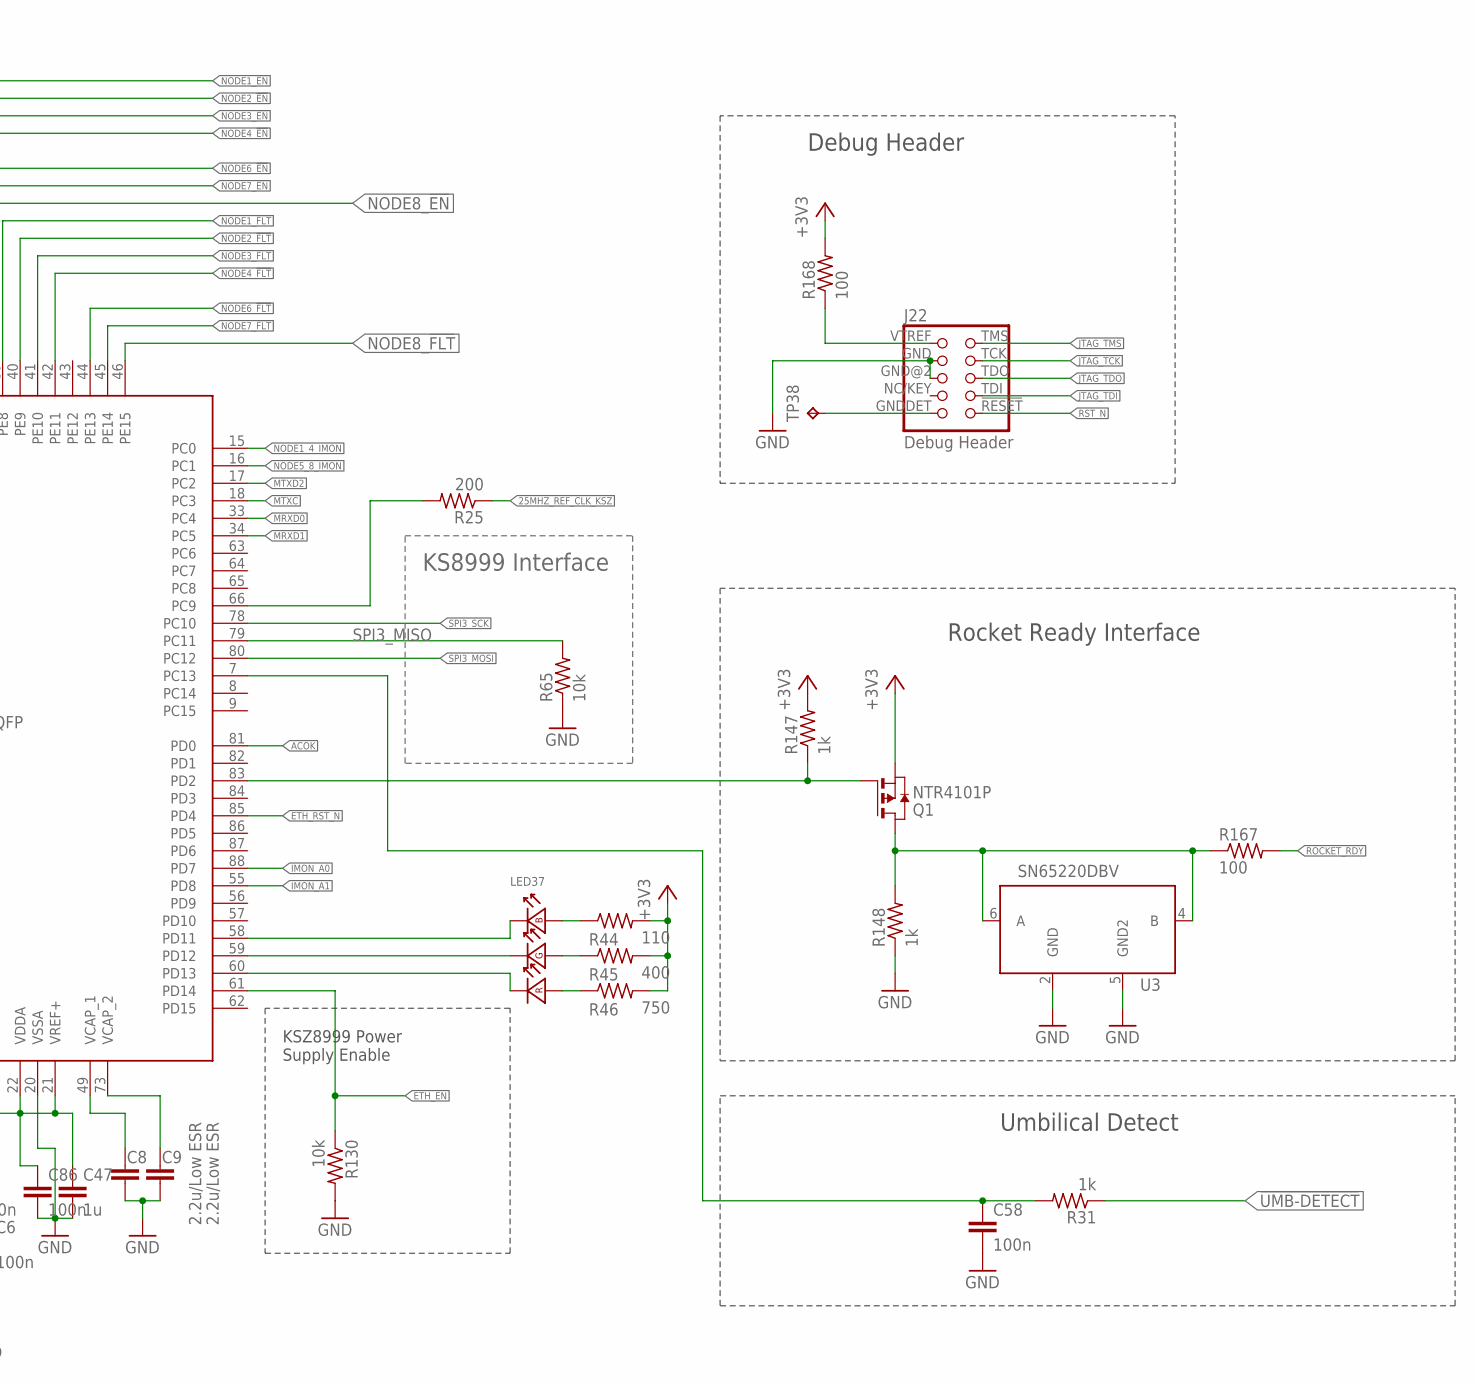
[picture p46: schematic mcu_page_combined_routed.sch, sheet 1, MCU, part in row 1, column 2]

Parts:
C1, C2, C3, C4, C5, C6, C58, C86: 100n; 0402-B-NOSILK
C8, C9: 2.2u/Low ESR; 0402-B-NOSILK
C46, C47: 1u; 0603-B-NOSILK
C106, C107: 10p; 0402-B-NOSILK
E5: TBD/FB; 0603-B
J5: BOOT0 Jumper; 1.27MM_2X1
J10: UART Header; INLINE
J11: I2C Header; 1.27MM_3X1
J12: BOOT1 Jumper; 1.27MM_2X1
J22: Debug Header; 1.27MM_2X5
LED37: LED_RGB_PLCC-6; PLCC-6
Q1: NTR4101P; SOT23
R12, R64, R65, R130, R150: 10k; 0402-B-NOSILK
R15, R17: 2.2k; 0402-B-NOSILK
R25: 200; 0402-B-NOSILK
R31, R147, R148: 1k; 0402-B-NOSILK
R44: 110; 0402-B-NOSILK
R45: 400; 0402-B-NOSILK
R46: 750; 0402-B-NOSILK
R167, R168: 100; 0402-B-NOSILK
TP36, TP37, TP38, TP39: TPTP06R; TP06R
U1: STM32F407V100-PIN_QFP; LQFP-100
U3: SN65220DBV; SOT23-6L
X1: 25 MHz; 8Y

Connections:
25MHZ_REF_CLK_KSZ: R25.1; also elsewhere on the board
25MHZ_REF_CLK_STM: R25.2, U1.66 (PC9)
!UMB-DETECT: R31.1; also elsewhere on the board
!UMB_DETECT_MCU: C58.1, R31.2, U1.7 (PC13)
+3V3: C1.1, C2.1, C3.1, C4.1, C5.1, C6.1, C46.1, E5.1, J5.2, J12.2, Q1.2 (S), R12.1, R15.1, R17.1, R44.2, R45.2, R46.2, R147.2, R168.2, U1.6 (VBAT), U1.11 (VDD1), U1.19 (VDD2), U1.28 (VDD3), U1.50 (VDD4), U1.75 (VDD5), U1.100 (VDD6); also elsewhere on the board
ACOK: U1.81 (PD0); also elsewhere on the board
BAT_IMON: U1.25 (PA2); also elsewhere on the board
BOOT0: J5.1, R64.1, U1.94 (BOOT0)
BOOT1: J12.1, R150.1, U1.37 (PB2)
ETH_EN: R130.1, U1.61 (PD14); also elsewhere on the board
ETH_RST_N: U1.85 (PD4); also elsewhere on the board
GND: C1.2, C2.2, C3.2, C4.2, C5.2, C6.2, C8.2, C9.2, C46.2, C47.2, C58.2, C86.2, C106.1, C107.1, J10.4 (GND), J11.3 (GND), J22.GND, J22.GND@2 (GND), R64.2, R65.1, R130.2, R148.1, R150.2, TP39.TP, U1.10 (VSS1), U1.20 (VSSA), U1.27 (VSS2), U1.47 (PB10), U1.74 (VSS3), U1.99 (VSS4), U3.2 (GND), U3.5 (GND2), X1.2 (3), X1.4 (3); also elsewhere on the board
IMON_A0: U1.88 (PD7); also elsewhere on the board
IMON_A1: U1.55 (PD8); also elsewhere on the board
JTAG_TCK: J22.TCK, U1.76 (PA14)
JTAG_TDI: J22.TDI, U1.77 (PA15)
JTAG_TDO: J22.TDO, U1.89 (PB3)
JTAG_TMS: J22.TMS, U1.72 (PA13)
JTAG_TRST: TP36.TP, U1.90 (PB4)
MCOL: U1.26 (PA3); also elsewhere on the board
MCRS: U1.23 (PA0); also elsewhere on the board
MRXC: U1.24 (PA1); also elsewhere on the board
MRXD0: U1.33 (PC4); also elsewhere on the board
MRXD1: U1.34 (PC5); also elsewhere on the board
MRXD2: U1.35 (PB0); also elsewhere on the board
MRXD3: U1.36 (PB1); also elsewhere on the board
MRXDV: U1.32 (PA7); also elsewhere on the board
MTXC: U1.18 (PC3); also elsewhere on the board
MTXD0: U1.51 (PB12); also elsewhere on the board
MTXD1: U1.52 (PB13); also elsewhere on the board
MTXD2: U1.17 (PC2); also elsewhere on the board
MTXD3: U1.95 (PB8); also elsewhere on the board
MTXEN: U1.48 (PB11); also elsewhere on the board
unnamed: C106.2, U1.13 (PH1), X1.1
unnamed: C8.1, U1.49 (VCAP_1)
unnamed: C107.2, U1.12 (PH0), X1.3 (2)
unnamed: Q1.3 (D), R148.2, R167.1, U3.4 (B), U3.6 (A)
unnamed: LED37.6 (K), U1.60 (PD13)
unnamed: LED37.2 (K), U1.59 (PD12)
unnamed: LED37.5 (K), U1.58 (PD11)
unnamed: LED37.1 (A), R46.1
unnamed: LED37.3 (A), R45.1
unnamed: LED37.4 (A), R44.1
unnamed: C47.1, C86.1, E5.2, U1.21 (VREF+), U1.22 (VDDA)
unnamed: C9.1, U1.73 (VCAP_2)
unnamed: J22.VTREF, R168.1
unnamed: J22.GNDDET, TP38.TP
NODE1_4_IMON: U1.15 (PC0); also elsewhere on the board
NODE1_!EN: U1.97 (PE0); also elsewhere on the board
NODE1_!FLT: U1.39 (PE8); also elsewhere on the board
NODE2_!EN: U1.98 (PE1); also elsewhere on the board
NODE2_!FLT: U1.40 (PE9); also elsewhere on the board
NODE3_!EN: U1.1 (PE2); also elsewhere on the board
NODE3_!FLT: U1.41 (PE10); also elsewhere on the board
NODE4_!EN: U1.2 (PE3); also elsewhere on the board
NODE4_!FLT: U1.42 (PE11); also elsewhere on the board
NODE5_8_IMON: U1.16 (PC1); also elsewhere on the board
NODE6_!EN: U1.4 (PE5); also elsewhere on the board
NODE6_!FLT: U1.44 (PE13); also elsewhere on the board
NODE7_!EN: U1.5 (PE6); also elsewhere on the board
NODE7_!FLT: U1.45 (PE14); also elsewhere on the board
NODE8_!EN: U1.38 (PE7); also elsewhere on the board
NODE8_!FLT: U1.46 (PE15); also elsewhere on the board
ROCKET_RDY: R167.2; also elsewhere on the board
ROCKET_RDY_MCU: Q1.1 (G), R147.1, U1.83 (PD2)
RST_N: J22.!RESET, R12.2, TP37.TP, U1.14 (NRST)
SCL: J11.1 (SCL), R17.2, U1.92 (PB6); also elsewhere on the board
SDA: J11.2 (SDA), R15.2, U1.93 (PB7); also elsewhere on the board
SPI3_MISO: R65.2, U1.79 (PC11)
SPI3_MOSI: U1.80 (PC12); also elsewhere on the board
SPI3_SCK: U1.78 (PC10); also elsewhere on the board
STM32_RX: J10.2 (STM32_RX), U1.69 (PA10)
STM32_TX: J10.1 (STM32_TX), U1.68 (PA9)
SYNC: U1.67 (PA8); also elsewhere on the board

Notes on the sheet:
Debug Header
Rocket Ready Interface
Boot Configuration
KSZ8999 Power Supply Enable
KS8999 Interface
UART Interface
Ferrite bead position before/after capacitors
Umbilical Detect

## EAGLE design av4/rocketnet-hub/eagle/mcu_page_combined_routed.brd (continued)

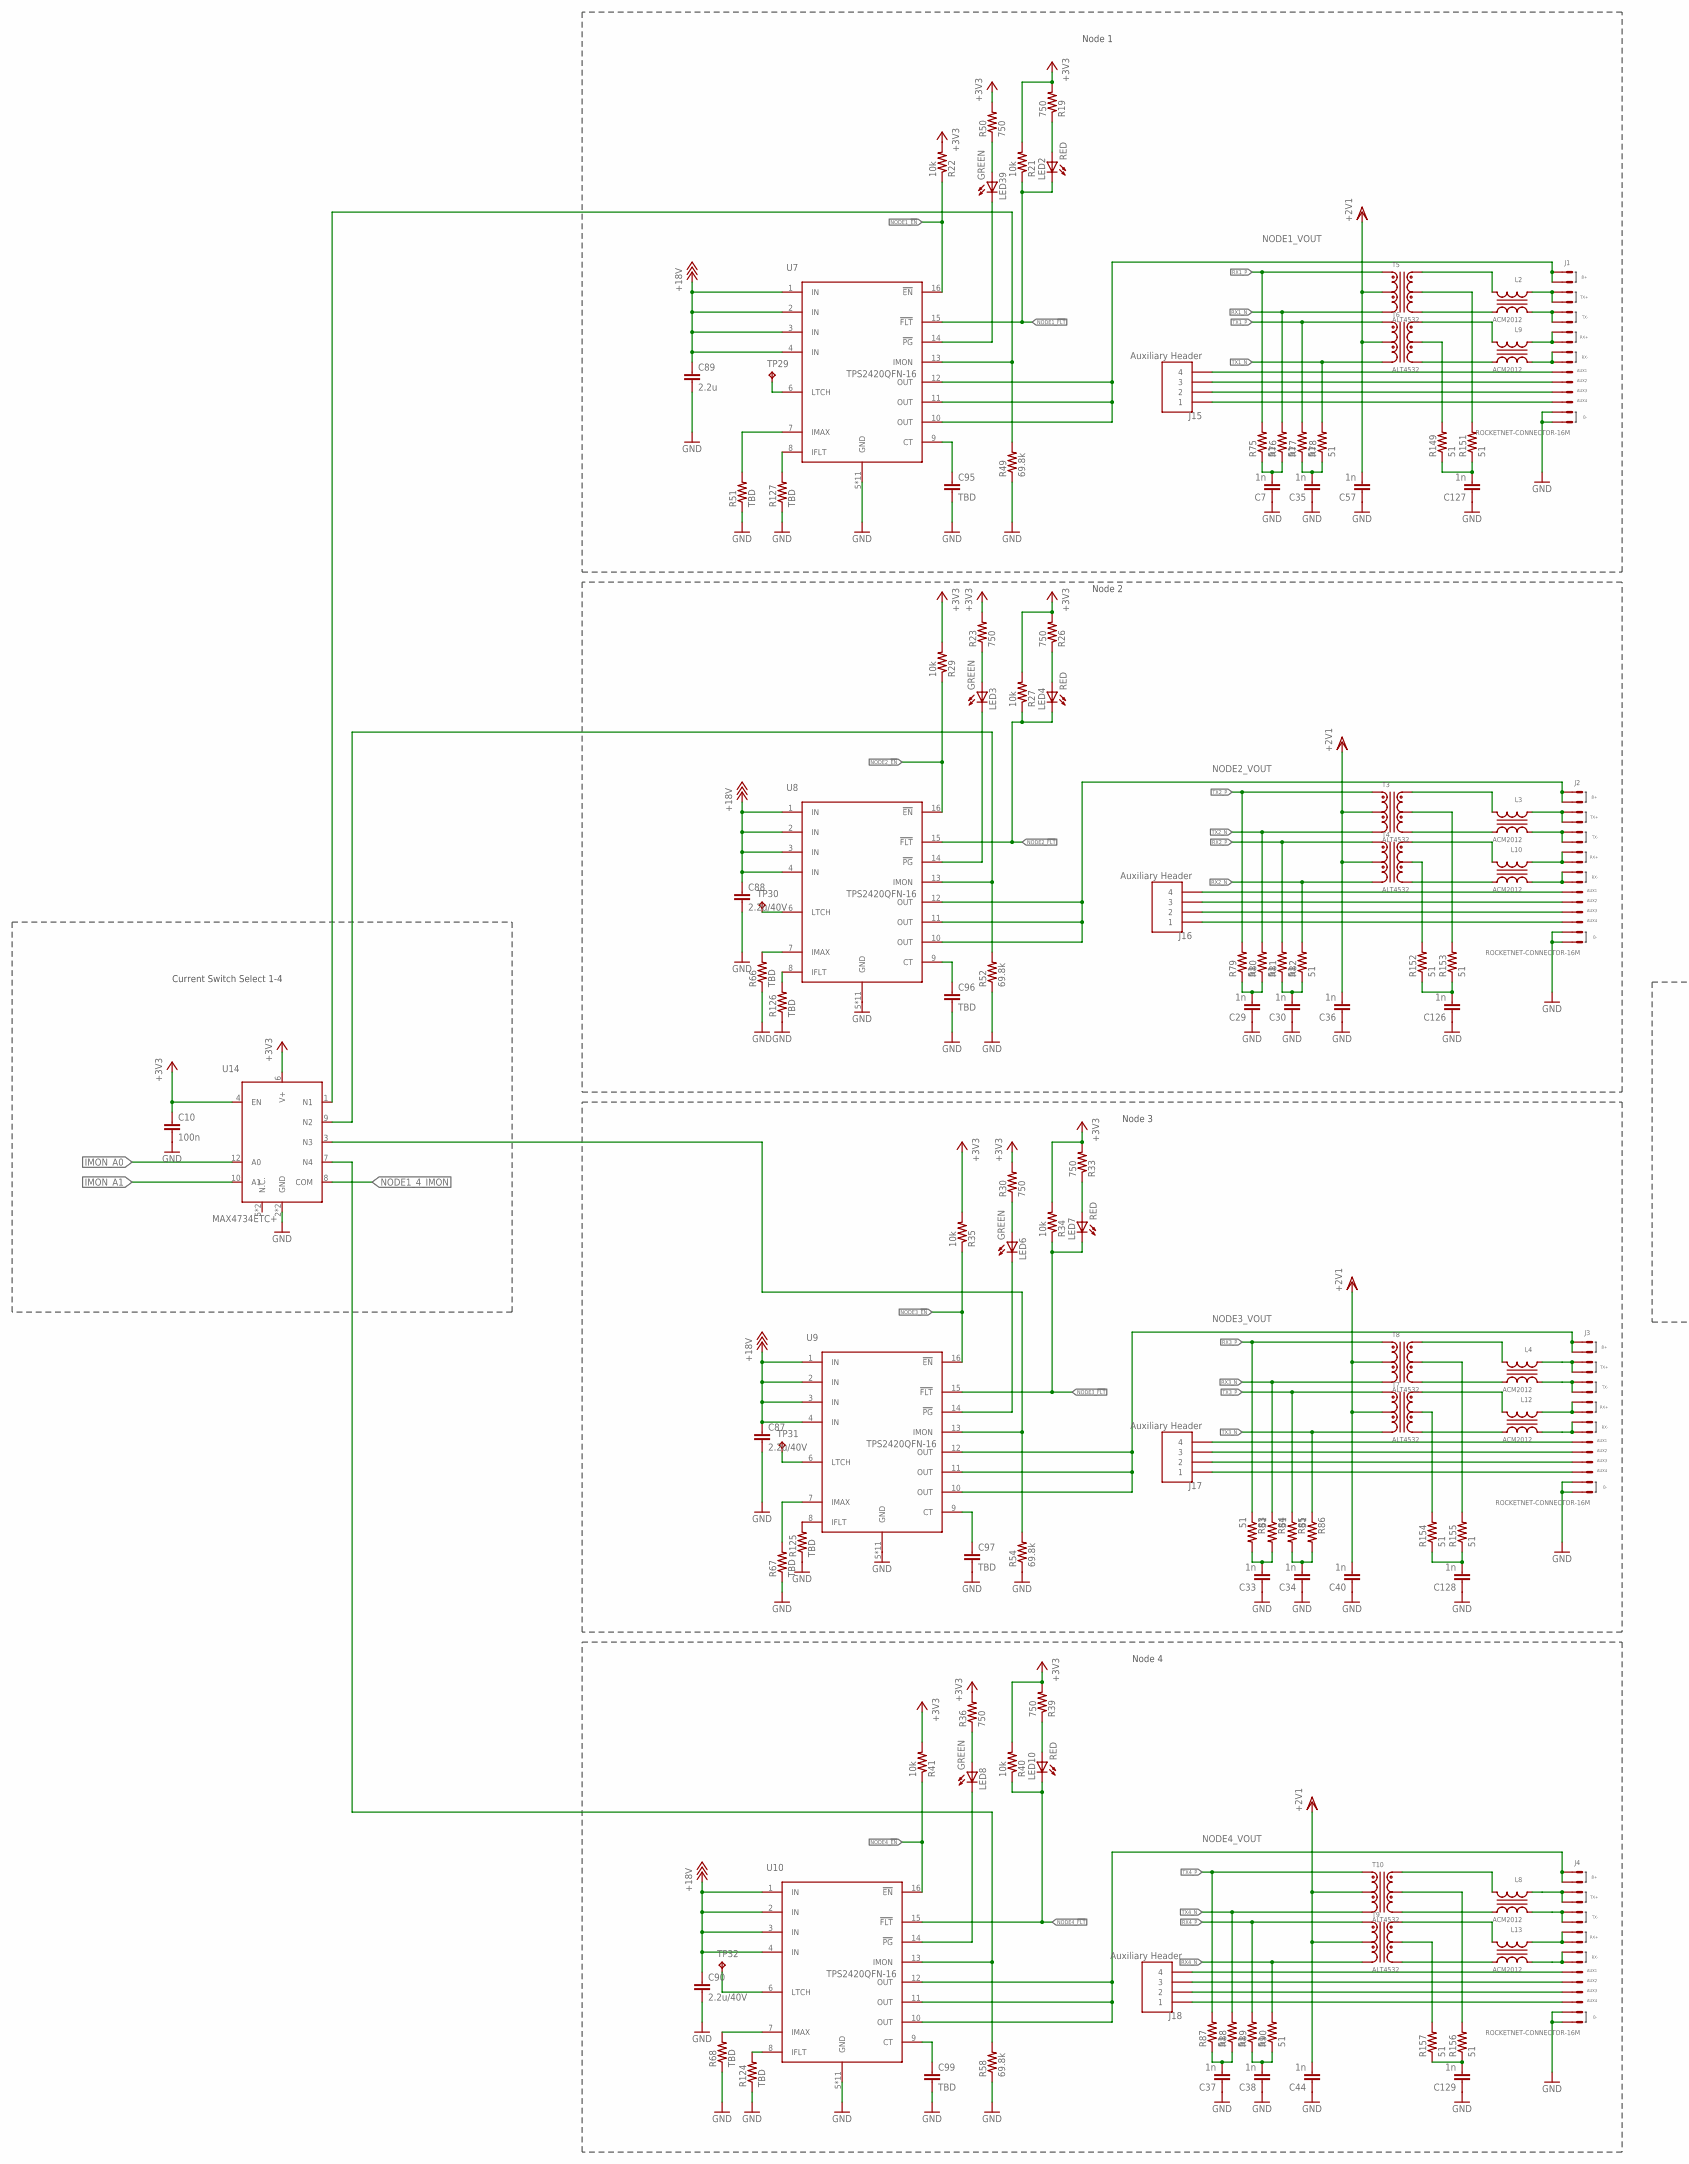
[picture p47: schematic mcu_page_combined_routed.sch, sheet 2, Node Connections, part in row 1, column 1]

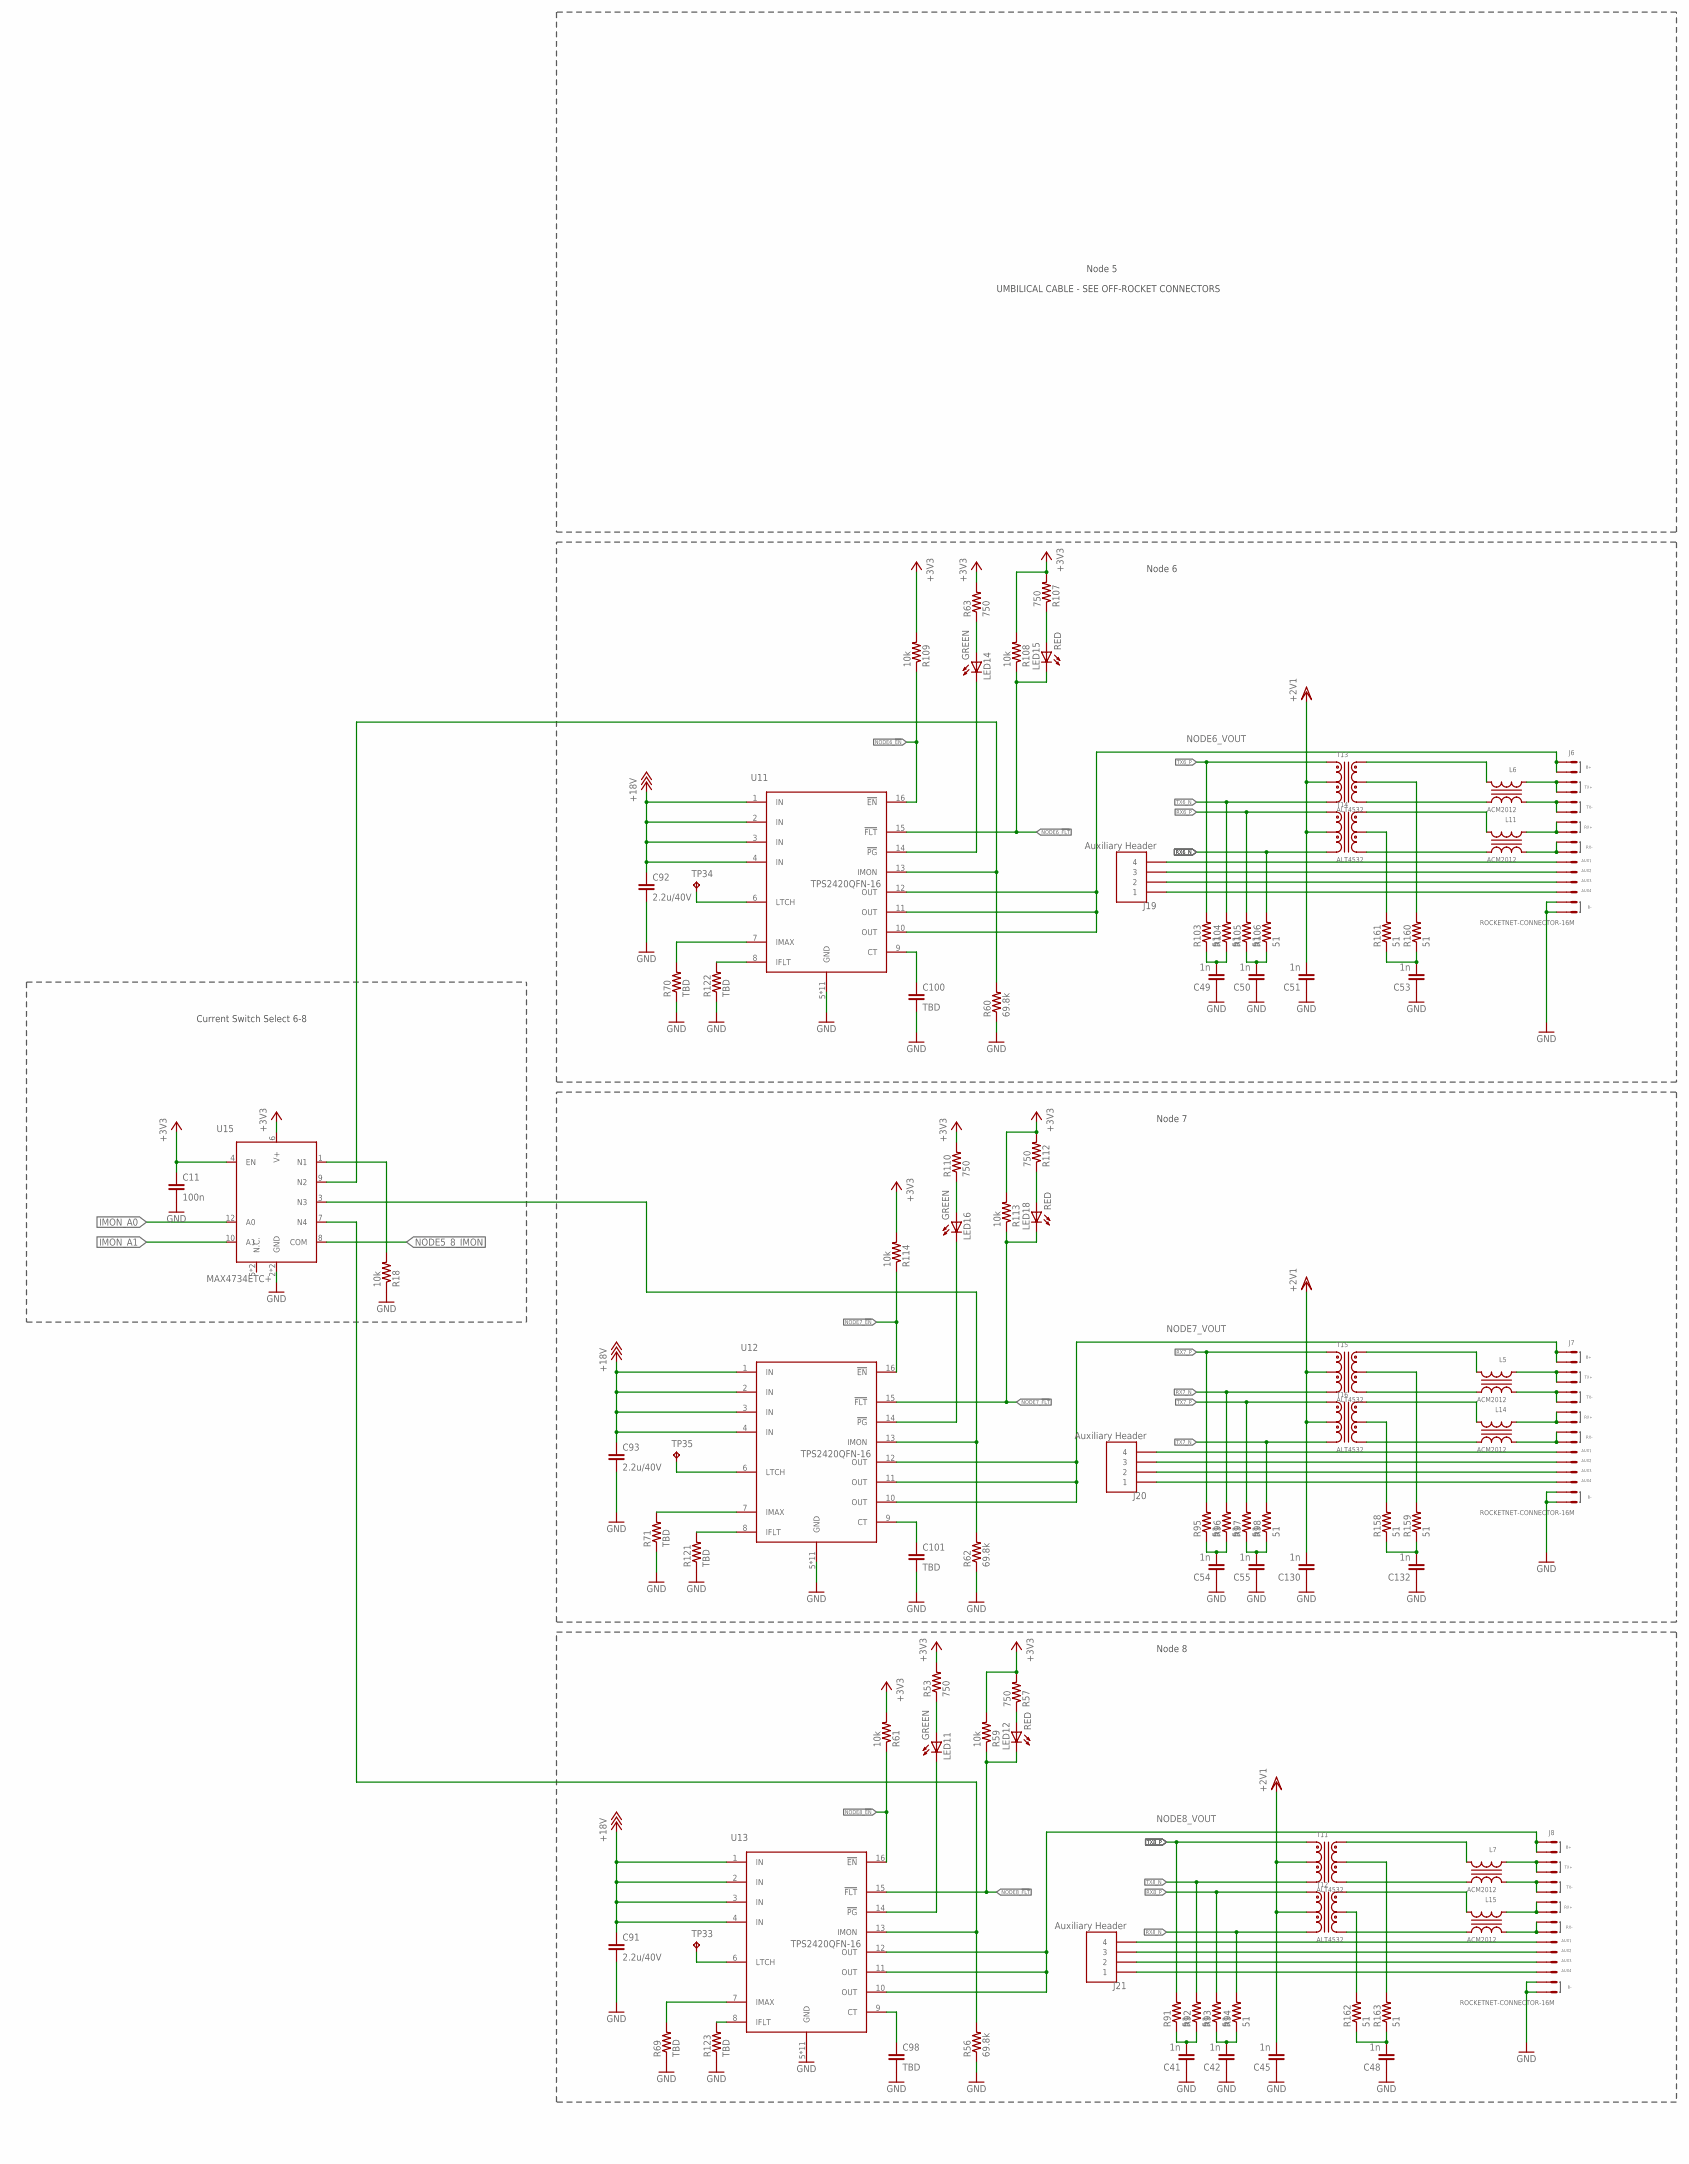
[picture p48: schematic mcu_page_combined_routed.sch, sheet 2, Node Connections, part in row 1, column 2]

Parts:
C7, C29, C30, C33, C34, C35, C36, C37, C38, C40, C41, C42, C44, C45, C48, C49, C50, C51, C53, C54, C55, C57, C126, C127, C128, C129, C130, C132: 1n; 0402-B-NOSILK
C10, C11: 100n; 0402-B-NOSILK
C87, C88, C90, C91, C92, C93: 2.2u/40V; 0603-B-NOSILK
C89: 2.2u; 0603-B-NOSILK
C95, C96, C97, C98, C99, C100, C101: TBD; 0402-B-NOSILK
J1, J2, J3, J4, J6, J7, J8: ROCKETNET-CONNECTOR-16M; ROCKETNET-M-16
J15, J16, J17, J18, J19, J20, J21: Auxiliary Header; INLINE
L2, L3, L4, L5, L6, L7, L8, L9, L10, L11, L12, L13, L14, L15: ACM2012; TDK-ACM2012
LED2, LED4, LED7, LED10, LED12, LED15, LED18: RED; CHIPLED_0603
LED3, LED6, LED8, LED11, LED14, LED16, LED39: GREEN; CHIPLED_0603
R18, R21, R22, R27, R29, R34, R35, R40, R41, R59, R61, R108, R109, R113, R114: 10k; 0402-B-NOSILK
R19, R23, R26, R30, R33, R36, R39, R50, R53, R57, R63, R107, R110, R112: 750; 0402-B-NOSILK
R49, R52, R54, R56, R58, R60, R62: 69.8k; 0402-B-NOSILK
R51, R66, R67, R68, R69, R70, R71, R121, R122, R123, R124, R125, R126, R127: TBD; 0402-B-NOSILK
R75, R76, R77, R78, R79, R80, R81, R82, R83, R84, R85, R86, R87, R88, R89, R90, R91, R92, R93, R94, R95, R96, R97, R98, R103, R104, R105, R106, R149, R151, R152, R153, R154, R155, R156, R157, R158, R159, R160, R161, R162, R163: 51; 0402-B-NOSILK
T3, T4, T5, T6, T7, T8, T9, T10, T11, T12, T13, T14, T15, T16: ALT4532; TDK-ALT4532
TP29, TP30, TP31, TP32, TP33, TP34, TP35: TPTP06R; TP06R
U7, U8, U9, U10, U11, U12, U13: TPS2420QFN-16; QFN-306
U14, U15: MAX4734ETC+; TQFN-12

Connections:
+2V1: C36.2, C40.2, C44.2, C45.2, C51.2, C57.2, C130.2, T3.6, T4.6, T5.6, T6.6, T7.6, T8.6, T9.6, T10.6, T11.6, T12.6, T13.6, T14.6, T15.6, T16.6; also elsewhere on the board
+3V3: C10.1, C11.1, R19.2, R21.2, R22.2, R23.2, R26.2, R27.2, R29.2, R30.2, R33.2, R34.2, R35.2, R36.2, R39.2, R40.2, R41.2, R50.2, R53.2, R57.2, R59.2, R61.2, R63.2, R107.2, R108.2, R109.2, R110.2, R112.2, R113.2, R114.2, U14.4 (EN), U14.6 (V+), U15.4 (EN), U15.6 (V+); also elsewhere on the board
+18V: C87.1, C88.1, C89.1, C90.1, C91.1, C92.1, C93.1, U7.1 (IN), U7.2 (IN), U7.3 (IN), U7.4 (IN), U8.1 (IN), U8.2 (IN), U8.3 (IN), U8.4 (IN), U9.1 (IN), U9.2 (IN), U9.3 (IN), U9.4 (IN), U10.1 (IN), U10.2 (IN), U10.3 (IN), U10.4 (IN), U11.1 (IN), U11.2 (IN), U11.3 (IN), U11.4 (IN), U12.1 (IN), U12.2 (IN), U12.3 (IN), U12.4 (IN), U13.1 (IN), U13.2 (IN), U13.3 (IN), U13.4 (IN); also elsewhere on the board
GND: C7.1, C10.2, C11.2, C29.1, C30.1, C33.1, C34.1, C35.1, C36.1, C37.1, C38.1, C40.1, C41.1, C42.1, C44.1, C45.1, C48.1, C49.1, C50.1, C51.1, C53.1, C54.1, C55.1, C57.1, C87.2, C88.2, C89.2, C90.2, C91.2, C92.2, C93.2, C95.2, C96.2, C97.2, C98.2, C99.2, C100.2, C101.2, C126.1, C127.1, C128.1, C129.1, C130.1, C132.1, J1.B-@1 (B-), J1.B-@2 (B-), J2.B-@1 (B-), J2.B-@2 (B-), J3.B-@1 (B-), J3.B-@2 (B-), J4.B-@1 (B-), J4.B-@2 (B-), J6.B-@1 (B-), J6.B-@2 (B-), J7.B-@1 (B-), J7.B-@2 (B-), J8.B-@1 (B-), J8.B-@2 (B-), R18.1, R49.1, R51.1, R52.1, R54.1, R56.1, R58.1, R60.1, R62.1, R66.1, R67.1, R68.1, R69.1, R70.1, R71.1, R121.1, R122.1, R123.1, R124.1, R125.1, R126.1, R127.1, U7.5 (GND), U7.DAP (GND), U7.P$2 (GND), U7.P$3 (GND), U7.P$4 (GND), U7.P$5 (GND), U7.P$6 (GND), U7.P$7 (GND), U7.P$8 (GND), U7.P$9 (GND), U7.P$10 (GND), U8.5 (GND), U8.DAP (GND), U8.P$2 (GND), U8.P$3 (GND), U8.P$4 (GND), U8.P$5 (GND), U8.P$6 (GND), U8.P$7 (GND), U8.P$8 (GND), U8.P$9 (GND), U8.P$10 (GND), U9.5 (GND), U9.DAP (GND), U9.P$2 (GND), U9.P$3 (GND), U9.P$4 (GND), U9.P$5 (GND), U9.P$6 (GND), U9.P$7 (GND), U9.P$8 (GND), U9.P$9 (GND), U9.P$10 (GND), U10.5 (GND), U10.DAP (GND), U10.P$2 (GND), U10.P$3 (GND), U10.P$4 (GND), U10.P$5 (GND), U10.P$6 (GND), U10.P$7 (GND), U10.P$8 (GND), U10.P$9 (GND), U10.P$10 (GND), U11.5 (GND), U11.DAP (GND), U11.P$2 (GND), U11.P$3 (GND), U11.P$4 (GND), U11.P$5 (GND), U11.P$6 (GND), U11.P$7 (GND), U11.P$8 (GND), U11.P$9 (GND), U11.P$10 (GND), U12.5 (GND), U12.DAP (GND), U12.P$2 (GND), U12.P$3 (GND), U12.P$4 (GND), U12.P$5 (GND), U12.P$6 (GND), U12.P$7 (GND), U12.P$8 (GND), U12.P$9 (GND), U12.P$10 (GND), U13.5 (GND), U13.DAP (GND), U13.P$2 (GND), U13.P$3 (GND), U13.P$4 (GND), U13.P$5 (GND), U13.P$6 (GND), U13.P$7 (GND), U13.P$8 (GND), U13.P$9 (GND), U13.P$10 (GND), U14.2 (GND), U14.P$13 (GND), U15.2 (GND), U15.P$13 (GND); also elsewhere on the board
IMON_A0: U14.12 (A0), U15.12 (A0); also elsewhere on the board
IMON_A1: U14.10 (A1), U15.10 (A1); also elsewhere on the board
unnamed: R51.2, U7.7 (IMAX)
unnamed: R66.2, U8.7 (IMAX)
unnamed: J4.T-@9 (TX-), J4.T-@11 (TX-), L8.2
unnamed: C33.2, R83.2, R84.2
unnamed: R18.2, U15.1 (N1)
unnamed: J1.T-@9 (TX-), J1.T-@11 (TX-), L2.2
unnamed: J1.T+@13 (TX+), J1.T+@14 (TX+), L2.1
unnamed: L4.4, T8.5
unnamed: L2.3, T5.4
unnamed: L8.4, T10.5
unnamed: L9.3, T6.4
unnamed: LED3.A, R23.1
unnamed: LED2.A, R19.1
unnamed: LED4.A, R26.1
unnamed: LED6.A, R30.1
unnamed: LED7.A, R33.1
unnamed: LED8.A, R36.1
unnamed: LED10.A, R39.1
unnamed: LED11.A, R53.1
unnamed: LED12.A, R57.1
unnamed: LED14.A, R63.1
unnamed: LED15.A, R107.1
unnamed: LED16.A, R110.1
unnamed: LED18.A, R112.1
unnamed: R121.2, U12.8 (IFLT)
unnamed: R122.2, U11.8 (IFLT)
unnamed: R123.2, U13.8 (IFLT)
unnamed: R124.2, U10.8 (IFLT)
unnamed: R126.2, U8.8 (IFLT)
unnamed: R127.2, U7.8 (IFLT)
unnamed: J1.R+@5 (RX+), J1.R+@7 (RX+), L9.1
unnamed: L10.3, T4.4
unnamed: J6.A1 (AUX1), J19.4
unnamed: L3.3, T3.4
unnamed: L9.4, T6.5
unnamed: L4.3, T8.4
unnamed: J8.T+@13 (TX+), J8.T+@14 (TX+), L7.1
unnamed: C127.2, R149.1, R151.1
unnamed: L12.3, T7.4
unnamed: J8.R-@3 (RX-), J8.R-@4 (RX-), L15.2
unnamed: L13.3, T9.4
unnamed: J6.T-@9 (TX-), J6.T-@11 (TX-), L6.2
unnamed: L13.4, T9.5
unnamed: R67.2, U9.7 (IMAX)
unnamed: LED39.A, R50.1
unnamed: C95.1, U7.9 (CT)
unnamed: L8.3, T10.4
unnamed: J7.R+@5 (RX+), J7.R+@7 (RX+), L14.1
unnamed: C34.2, R85.2, R86.2
unnamed: L14.3, T16.4
unnamed: J2.R+@5 (RX+), J2.R+@7 (RX+), L10.1
unnamed: R125.2, U9.8 (IFLT)
unnamed: C96.1, U8.9 (CT)
unnamed: C98.1, U13.9 (CT)
unnamed: C99.1, U10.9 (CT)
unnamed: C100.1, U11.9 (CT)
unnamed: C101.1, U12.9 (CT)
unnamed: R68.2, U10.7 (IMAX)
unnamed: R69.2, U13.7 (IMAX)
unnamed: R70.2, U11.7 (IMAX)
unnamed: R71.2, U12.7 (IMAX)
unnamed: LED39.C, U7.14 (!PG)
unnamed: L5.3, T15.4
unnamed: C55.2, R97.1, R98.1
unnamed: C30.2, R81.1, R82.1
unnamed: R152.2, T4.3
unnamed: R153.2, T3.3
unnamed: C29.2, R79.1, R80.1
unnamed: R149.2, T6.3
unnamed: R151.2, T5.3
unnamed: J7.R-@3 (RX-), J7.R-@4 (RX-), L14.2
unnamed: C37.2, R87.1, R88.1
unnamed: R154.2, T7.3
unnamed: R155.2, T8.3
unnamed: C38.2, R89.1, R90.1
unnamed: C48.2, R162.1, R163.1
unnamed: R157.2, T9.3
unnamed: R156.2, T10.3
unnamed: L6.3, T13.4
unnamed: J6.R-@3 (RX-), J6.R-@4 (RX-), L11.2
unnamed: L11.3, T14.4
unnamed: J7.T+@13 (TX+), J7.T+@14 (TX+), L5.1
unnamed: C41.2, R91.1, R92.1
unnamed: C42.2, R93.1, R94.1
unnamed: R162.2, T12.3
unnamed: R163.2, T11.3
unnamed: C49.2, R103.1, R104.1
unnamed: C50.2, R105.1, R106.1
unnamed: R161.2, T14.3
unnamed: R160.2, T13.3
unnamed: C54.2, R95.1, R96.1
unnamed: C7.2, R75.1, R76.1
unnamed: R158.2, T16.3
unnamed: R159.2, T15.3
unnamed: C126.2, R152.1, R153.1
unnamed: C128.2, R154.1, R155.1
unnamed: C129.2, R156.1, R157.1
unnamed: C132.2, R158.1, R159.1
unnamed: LED3.C, U8.14 (!PG)
unnamed: C53.2, R160.1, R161.1
unnamed: C35.2, R77.1, R78.1
unnamed: LED6.C, U9.14 (!PG)
unnamed: L2.4, T5.5
unnamed: L15.3, T12.4
unnamed: J8.T-@9 (TX-), J8.T-@11 (TX-), L7.2
unnamed: J6.T+@13 (TX+), J6.T+@14 (TX+), L6.1
unnamed: J7.T-@9 (TX-), J7.T-@11 (TX-), L5.2
unnamed: J3.T-@9 (TX-), J3.T-@11 (TX-), L4.2
unnamed: J3.T+@13 (TX+), J3.T+@14 (TX+), L4.1
unnamed: J2.T-@9 (TX-), J2.T-@11 (TX-), L3.2
unnamed: J2.T+@13 (TX+), J2.T+@14 (TX+), L3.1
unnamed: J4.T+@13 (TX+), J4.T+@14 (TX+), L8.1
unnamed: L5.4, T15.5
unnamed: L6.4, T13.5
unnamed: L7.4, T11.5
unnamed: L3.4, T3.5
unnamed: J1.R-@3 (RX-), J1.R-@4 (RX-), L9.2
unnamed: J3.R-@3 (RX-), J3.R-@4 (RX-), L12.2
unnamed: J2.R-@3 (RX-), J2.R-@4 (RX-), L10.2
unnamed: J3.R+@5 (RX+), J3.R+@7 (RX+), L12.1
unnamed: L7.3, T11.4
unnamed: J6.R+@5 (RX+), J6.R+@7 (RX+), L11.1
unnamed: J8.R+@5 (RX+), J8.R+@7 (RX+), L15.1
unnamed: L10.4, T4.5
unnamed: L12.4, T7.5
unnamed: J4.R-@3 (RX-), J4.R-@4 (RX-), L13.2
unnamed: J4.R+@5 (RX+), J4.R+@7 (RX+), L13.1
unnamed: L14.4, T16.5
unnamed: L11.4, T14.5
unnamed: L15.4, T12.5
unnamed: TP32.TP, U10.6 (LTCH)
unnamed: LED8.C, U10.14 (!PG)
unnamed: LED14.C, U11.14 (!PG)
unnamed: LED16.C, U12.14 (!PG)
NODE1_4_IMON: U14.8 (COM); also elsewhere on the board
NODE1_!EN: R22.1, U7.16 (!EN); also elsewhere on the board
NODE1_!FLT: LED2.C, R21.1, U7.15 (!FLT); also elsewhere on the board
NODE1_IMON_IN: R49.2, U7.13 (IMON), U14.1 (N1)
NODE1_LTCH: TP29.TP, U7.6 (LTCH)
NODE1_RSV1: J1.A4 (AUX4), J15.1
NODE1_RSV2: J1.A2 (AUX2), J15.3
NODE1_RSV3: J1.A3 (AUX3), J15.2
NODE1_RSV4: J1.A1 (AUX1), J15.4
NODE1_VOUT: J1.B+@15 (B+), J1.B+@16 (B+), U7.10 (OUT), U7.11 (OUT), U7.12 (OUT)
NODE2_!EN: R29.1, U8.16 (!EN); also elsewhere on the board
NODE2_!FLT: LED4.C, R27.1, U8.15 (!FLT); also elsewhere on the board
NODE2_IMON_IN: R52.2, U8.13 (IMON), U14.9 (N2)
NODE2_LTCH: TP30.TP, U8.6 (LTCH)
NODE2_RSV1: J2.A4 (AUX4), J16.1
NODE2_RSV2: J2.A2 (AUX2), J16.3
NODE2_RSV3: J2.A3 (AUX3), J16.2
NODE2_RSV4: J2.A1 (AUX1), J16.4
NODE2_VOUT: J2.B+@15 (B+), J2.B+@16 (B+), U8.10 (OUT), U8.11 (OUT), U8.12 (OUT)
NODE3_!EN: R35.1, U9.16 (!EN); also elsewhere on the board
NODE3_!FLT: LED7.C, R34.1, U9.15 (!FLT); also elsewhere on the board
NODE3_IMON_IN: R54.2, U9.13 (IMON), U14.3 (N3)
NODE3_LTCH: TP31.TP, U9.6 (LTCH)
NODE3_RSV1: J3.A4 (AUX4), J17.1
NODE3_RSV2: J3.A2 (AUX2), J17.3
NODE3_RSV3: J3.A3 (AUX3), J17.2
NODE3_RSV4: J3.A1 (AUX1), J17.4
NODE3_VOUT: J3.B+@15 (B+), J3.B+@16 (B+), U9.10 (OUT), U9.11 (OUT), U9.12 (OUT)
NODE4_!EN: R41.1, U10.16 (!EN); also elsewhere on the board
NODE4_!FLT: LED10.C, R40.1, U10.15 (!FLT); also elsewhere on the board
NODE4_IMON_IN: R58.2, U10.13 (IMON), U14.7 (N4)
NODE4_RSV: J4.A1 (AUX1), J18.4
NODE4_RSV1: J4.A4 (AUX4), J18.1
NODE4_RSV2: J4.A2 (AUX2), J18.3
NODE4_RSV3: J4.A3 (AUX3), J18.2
NODE4_VOUT: J4.B+@15 (B+), J4.B+@16 (B+), U10.10 (OUT), U10.11 (OUT), U10.12 (OUT)
NODE5_8_IMON: U15.8 (COM); also elsewhere on the board
NODE5_!PG: LED11.C, U13.14 (!PG)
NODE5_LTCH: TP33.TP, U13.6 (LTCH)
NODE6_!EN: R109.1, U11.16 (!EN); also elsewhere on the board
NODE6_!FLT: LED15.C, R108.1, U11.15 (!FLT); also elsewhere on the board
NODE6_IMON: R60.2, U11.13 (IMON), U15.9 (N2)
NODE6_LTCH: TP34.TP, U11.6 (LTCH)
NODE6_RSV2: J6.A2 (AUX2), J19.3
NODE6_RSV3: J6.A3 (AUX3), J19.2
NODE6_RSV21: J6.A4 (AUX4), J19.1
NODE6_VOUT: J6.B+@15 (B+), J6.B+@16 (B+), U11.10 (OUT), U11.11 (OUT), U11.12 (OUT)
NODE7_!EN: R114.1, U12.16 (!EN); also elsewhere on the board
NODE7_!FLT: LED18.C, R113.1, U12.15 (!FLT); also elsewhere on the board
NODE7_IMON: R62.2, U12.13 (IMON), U15.3 (N3)
NODE7_LTCH: TP35.TP, U12.6 (LTCH)
NODE7_RSV1: J7.A4 (AUX4), J20.1
NODE7_RSV2: J7.A2 (AUX2), J20.3
NODE7_RSV3: J7.A3 (AUX3), J20.2
NODE7_RSV4: J7.A1 (AUX1), J20.4
NODE7_VOUT: J7.B+@15 (B+), J7.B+@16 (B+), U12.10 (OUT), U12.11 (OUT), U12.12 (OUT)
NODE8_!EN: R61.1, U13.16 (!EN); also elsewhere on the board
NODE8_!FLT: LED12.C, R59.1, U13.15 (!FLT); also elsewhere on the board
NODE8_IMON: R56.2, U13.13 (IMON), U15.7 (N4)
NODE8_RSV1: J8.A4 (AUX4), J21.1
NODE8_RSV2: J8.A2 (AUX2), J21.3
NODE8_RSV3: J8.A3 (AUX3), J21.2
NODE8_RSV4: J8.A1 (AUX1), J21.4
NODE8_VOUT: J8.B+@15 (B+), J8.B+@16 (B+), U13.10 (OUT), U13.11 (OUT), U13.12 (OUT)
RATSNET: C97.1, U9.9 (CT)
RX1_N: R76.2, T5.2; also elsewhere on the board
RX1_P: R75.2, T5.1; also elsewhere on the board
RX2_N: R82.2, T4.2; also elsewhere on the board
RX2_P: R81.2, T4.1; also elsewhere on the board
RX3_N: R84.1, T8.2; also elsewhere on the board
RX3_P: R83.1, T8.1; also elsewhere on the board
RX4_N: R90.2, T9.2; also elsewhere on the board
RX4_P: R89.2, T9.1; also elsewhere on the board
RX6_N: R106.2, T14.2; also elsewhere on the board
RX6_P: R105.2, T14.1; also elsewhere on the board
RX7_N: R96.2, T15.2; also elsewhere on the board
RX7_P: R95.2, T15.1; also elsewhere on the board
RX8_N: R94.2, T12.2; also elsewhere on the board
RX8_P: R93.2, T12.1; also elsewhere on the board
TX1_N: R78.2, T6.2; also elsewhere on the board
TX1_P: R77.2, T6.1; also elsewhere on the board
TX2_N: R80.2, T3.2; also elsewhere on the board
TX2_P: R79.2, T3.1; also elsewhere on the board
TX3_N: R86.1, T7.2; also elsewhere on the board
TX3_P: R85.1, T7.1; also elsewhere on the board
TX4_N: R88.2, T10.2; also elsewhere on the board
TX4_P: R87.2, T10.1; also elsewhere on the board
TX6_N: R104.2, T13.2; also elsewhere on the board
TX6_P: R103.2, T13.1; also elsewhere on the board
TX7_N: R98.2, T16.2; also elsewhere on the board
TX7_P: R97.2, T16.1; also elsewhere on the board
TX8_N: R92.2, T11.2; also elsewhere on the board
TX8_P: R91.2, T11.1; also elsewhere on the board

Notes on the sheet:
Current Switch Select 1-4
Current Switch Select 6-8
Node 5
Node 1
Node 2
Node 3
Node 4
Node 6
Node 7
Node 8
UMBILICAL CABLE - SEE OFF-ROCKET CONNECTORS

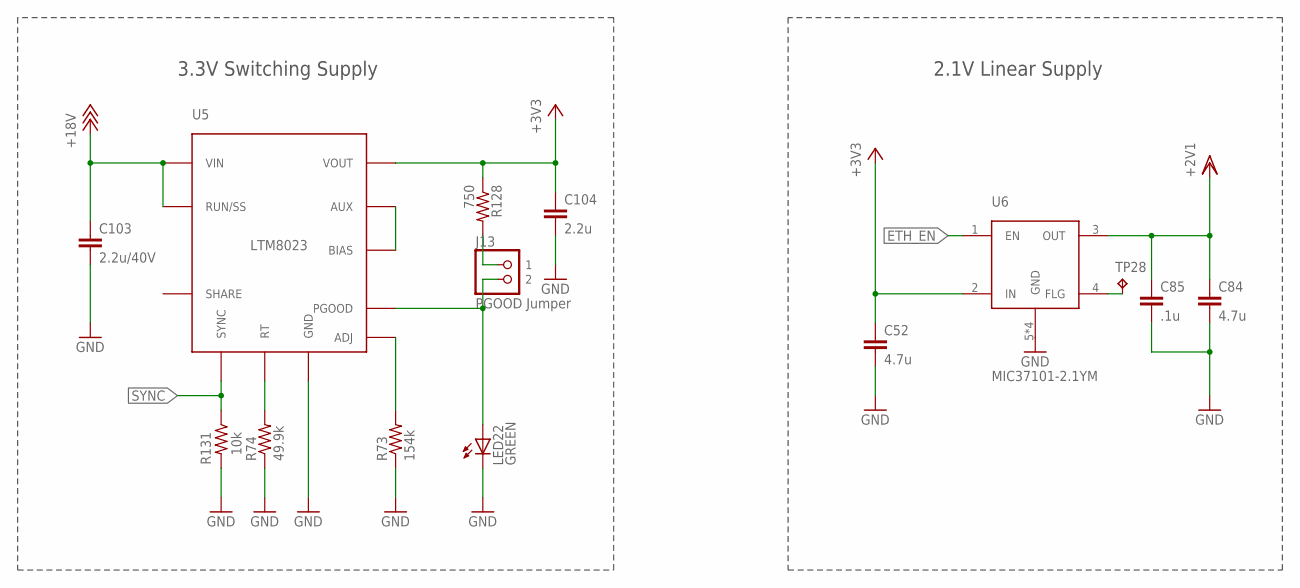
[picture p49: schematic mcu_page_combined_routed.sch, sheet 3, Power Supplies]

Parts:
C52: 4.7u; 0603-B-NOSILK
C84: 4.7u; 1206-B
C85: .1u; 0402-B-NOSILK
C103: 2.2u/40V; 0603-B-NOSILK
C104: 2.2u; 0603-B-NOSILK
J13: PGOOD Jumper; 1.27MM_2X1
LED22: GREEN; CHIPLED_0603
R73: 154k; 0402-B-NOSILK
R74: 49.9k; 0402-B-NOSILK
R128: 750; 0402-B-NOSILK
R131: 10k; 0402-B-NOSILK
TP28: TPTP06R; TP06R
U5: LTM8023; LGA-50
U6: MIC37101-2.1YM; SOIC-8

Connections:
+2V1: C84.1, C85.1, U6.3 (OUT); also elsewhere on the board
+3V3: C52.1, C104.1, R128.1, U5.VOUT@1 (VOUT), U5.VOUT@2 (VOUT), U5.VOUT@3 (VOUT), U5.VOUT@4 (VOUT), U5.VOUT@5 (VOUT), U5.VOUT@6 (VOUT), U5.VOUT@7 (VOUT), U5.VOUT@8 (VOUT), U5.VOUT@9 (VOUT), U5.VOUT@10 (VOUT), U5.VOUT@11 (VOUT), U5.VOUT@12 (VOUT), U6.2 (IN); also elsewhere on the board
+18V: C103.1, U5.RUN/SS, U5.VIN@1 (VIN), U5.VIN@2 (VIN), U5.VIN@3 (VIN), U5.VIN@4 (VIN), U5.VIN@5 (VIN), U5.VIN@6 (VIN); also elsewhere on the board
ETH_EN: U6.1 (EN); also elsewhere on the board
GND: C52.2, C84.2, C85.2, C103.2, C104.2, LED22.C, R73.1, R74.1, R131.2, U5.GND@1 (GND), U5.GND@2 (GND), U5.GND@3 (GND), U5.GND@4 (GND), U5.GND@5 (GND), U5.GND@6 (GND), U5.GND@7 (GND), U5.GND@8 (GND), U5.GND@9 (GND), U5.GND@10 (GND), U5.GND@11 (GND), U5.GND@12 (GND), U5.GND@13 (GND), U5.GND@14 (GND), U5.GND@15 (GND), U5.GND@16 (GND), U5.GND@17 (GND), U5.GND@18 (GND), U5.GND@19 (GND), U5.GND@20 (GND), U5.GND@21 (GND), U5.GND@22 (GND), U5.GND@23 (GND), U5.GND@24 (GND), U6.5 (GND), U6.6 (GND), U6.7 (GND), U6.8 (GND); also elsewhere on the board
unnamed: TP28.TP, U6.4 (FLG)
unnamed: J13.2, LED22.A, U5.PGOOD
unnamed: J13.1, R128.2
unnamed: U5.AUX, U5.BIAS
unnamed: R73.2, U5.ADJ
unnamed: R74.2, U5.RT
SYNC: R131.1, U5.SYNC; also elsewhere on the board

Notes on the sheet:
3.3V Switching Supply
2.1V Linear Supply

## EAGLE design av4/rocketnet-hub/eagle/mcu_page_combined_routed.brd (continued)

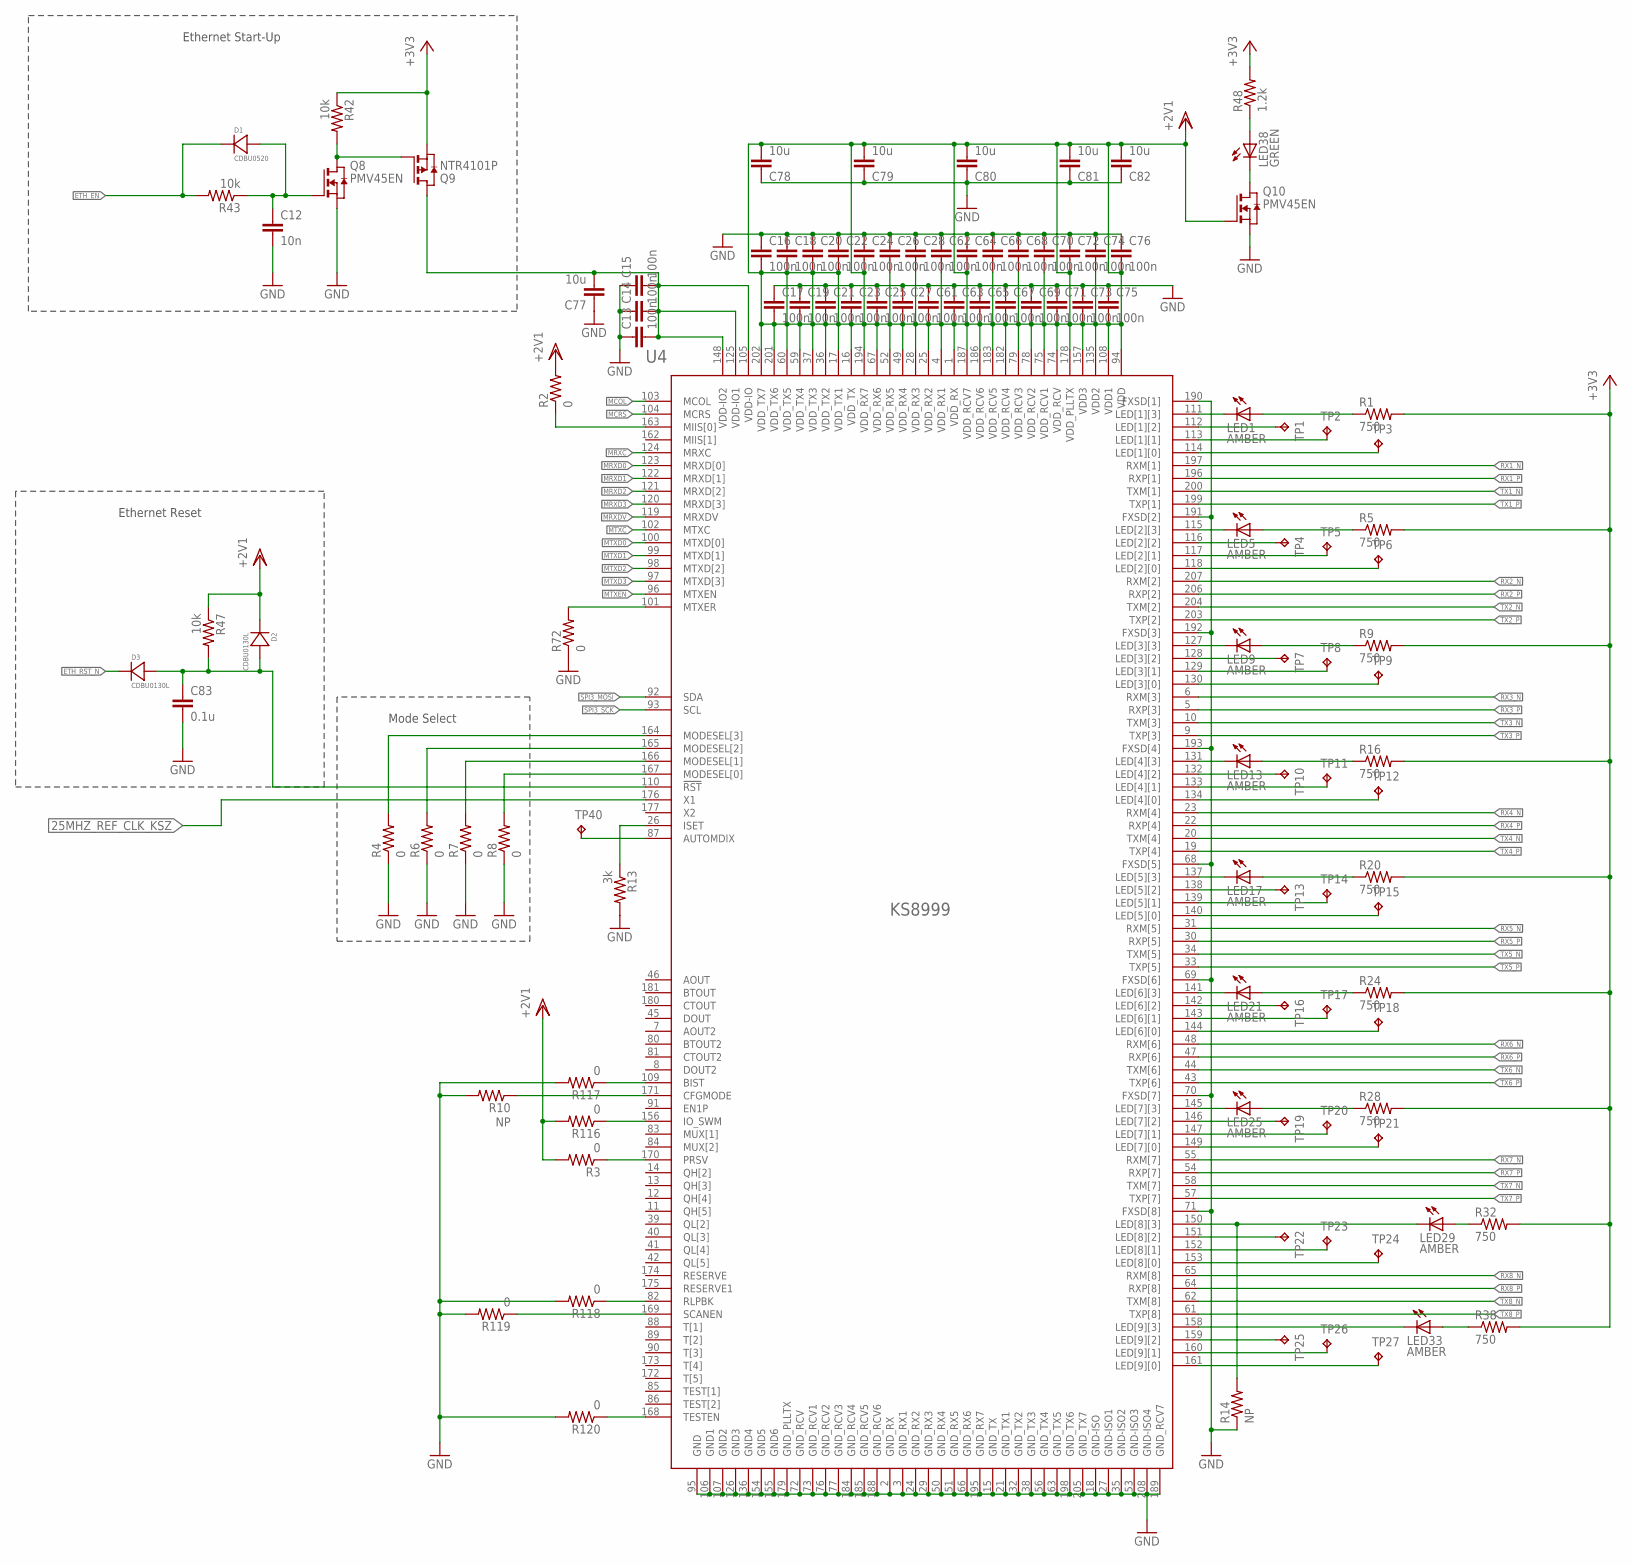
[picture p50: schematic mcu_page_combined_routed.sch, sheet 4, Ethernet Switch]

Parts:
C12: 10n; 0402-B-NOSILK
C13, C14, C15, C16, C17, C18, C19, C20, C21, C22, C23, C24, C25, C26, C27, C28, C61, C62, C63, C64, C65, C66, C67, C68, C69, C70, C71, C72, C73, C74, C75, C76: 100n; 0402-B-NOSILK
C77, C78, C79, C80, C81, C82: 10u; 0603-A-NOSILK
C83: 0.1u; 0402-B-NOSILK
D1: CDBU0520; 0603-B-NOSILK-DIODE
D2, D3: CDBU0130L; 0603-B-NOSILK-DIODE
LED1, LED5, LED9, LED13, LED17, LED21, LED25, LED29, LED33: AMBER; CHIPLED_0603
LED38: GREEN; CHIPLED_0603
Q8: PMV45EN; SOT23
Q9: NTR4101P; SOT23
Q10: PMV45EN; SOT-23
R1, R5, R9, R16, R20, R24, R28, R32, R38: 750; 0402-B-NOSILK
R2, R3, R4, R6, R7, R8, R72, R116, R117, R118, R119, R120: 0; 0402-B-NOSILK
R10, R14: NP; 0402-B-NOSILK
R13: 3k; 0402-B-NOSILK
R42, R43, R47: 10k; 0402-B-NOSILK
R48: 1.2k; 0402-B-NOSILK
TP1, TP2, TP3, TP4, TP5, TP6, TP7, TP8, TP9, TP10, TP11, TP12, TP13, TP14, TP15, TP16, TP17, TP18, TP19, TP20, TP21, TP22, TP23, TP24, TP25, TP26, TP27, TP40: TPTP06R; TP06R
U4: KS8999; PQFP208

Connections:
25MHZ_REF_CLK_KSZ: U4.176 (X1); also elsewhere on the board
+2V1: C16.2, C17.2, C18.2, C19.2, C20.2, C21.2, C22.2, C23.2, C24.2, C25.2, C26.2, C27.2, C28.2, C61.2, C62.2, C63.2, C64.2, C65.2, C66.2, C67.2, C68.2, C69.2, C70.2, C71.2, C72.2, C73.2, C74.2, C75.2, C76.2, C78.2, C79.2, C80.2, C81.2, C82.2, D2.CATHODE, Q10.3 (G), R2.2, R3.2, R47.1, R116.2, U4.1 (VDD_RX), U4.4 (VDD_RX1), U4.16 (VDD_TX), U4.17 (VDD_TX1), U4.25 (VDD_RX2), U4.28 (VDD_RX3), U4.36 (VDD_TX2), U4.37 (VDD_TX3), U4.49 (VDD_RX4), U4.52 (VDD_RX5), U4.59 (VDD_TX4), U4.60 (VDD_TX5), U4.67 (VDD_RX6), U4.74 (VDD_RCV), U4.75 (VDD_RCV1), U4.78 (VDD_RCV2), U4.79 (VDD_RCV3), U4.94 (VDD), U4.108 (VDD1), U4.135 (VDD2), U4.157 (VDD3), U4.178 (VDD_PLLTX), U4.182 (VDD_RCV4), U4.183 (VDD_RCV5), U4.186 (VDD_RCV6), U4.187 (VDD_RCV7), U4.194 (VDD_RX7), U4.201 (VDD_TX6), U4.202 (VDD_TX7); also elsewhere on the board
+3V3: Q9.2 (S), R1.2, R5.2, R9.2, R16.2, R20.2, R24.2, R28.2, R32.2, R38.2, R42.1, R48.2; also elsewhere on the board
ETH_EN: D1.CATHODE, R43.2; also elsewhere on the board
ETH_RST_N: D3.CATHODE; also elsewhere on the board
GND: C12.2, C13.1, C14.1, C15.1, C16.1, C17.1, C18.1, C19.1, C20.1, C21.1, C22.1, C23.1, C24.1, C25.1, C26.1, C27.1, C28.1, C61.1, C62.1, C63.1, C64.1, C65.1, C66.1, C67.1, C68.1, C69.1, C70.1, C71.1, C72.1, C73.1, C74.1, C75.1, C76.1, C77.1, C78.1, C79.1, C80.1, C81.1, C82.1, C83.2, Q8.2 (S), Q10.2 (S), R4.1, R6.1, R7.1, R8.1, R10.2, R13.2, R14.1, R72.1, R117.2, R118.2, R119.2, R120.2, U4.2 (GND_RX), U4.3 (GND_RX1), U4.15 (GND_TX), U4.18 (GND-ISO), U4.21 (GND_TX1), U4.24 (GND_RX2), U4.27 (GND-ISO1), U4.29 (GND_RX3), U4.32 (GND_TX2), U4.35 (GND-ISO2), U4.38 (GND_TX3), U4.50 (GND_RX4), U4.51 (GND_RX5), U4.53 (GND-ISO3), U4.56 (GND_TX4), U4.63 (GND_TX5), U4.66 (GND_RX6), U4.68 (FXSD[5]), U4.69 (FXSD[6]), U4.70 (FXSD[7]), U4.71 (FXSD[8]), U4.72 (GND_RCV), U4.73 (GND_RCV1), U4.76 (GND_RCV2), U4.77 (GND_RCV3), U4.95 (GND), U4.106 (GND1), U4.107 (GND2), U4.126 (GND3), U4.136 (GND4), U4.154 (GND5), U4.155 (GND6), U4.179 (GND_PLLTX), U4.184 (GND_RCV4), U4.185 (GND_RCV5), U4.188 (GND_RCV6), U4.189 (GND_RCV7), U4.190 (FXSD[1]), U4.191 (FXSD[2]), U4.192 (FXSD[3]), U4.193 (FXSD[4]), U4.195 (GND_RX7), U4.198 (GND_TX6), U4.205 (GND_TX7), U4.208 (GND-ISO4); also elsewhere on the board
LED1-3: LED1.C, U4.111 (LED[1][3])
LED2-3: LED5.C, U4.115 (LED[2][3])
LED3-3: LED9.C, U4.127 (LED[3][3])
LED4-3: LED13.C, U4.131 (LED[4][3])
LED5-3: LED17.C, U4.137 (LED[5][3])
LED6-3: LED21.C, U4.141 (LED[6][3])
LED7-3: LED25.C, U4.145 (LED[7][3])
LED8-3: LED29.C, R14.2, U4.150 (LED[8][3])
LED9-3: LED33.C, U4.158 (LED[9][3])
MCOL: U4.103 (MCOL); also elsewhere on the board
MCRS: U4.104 (MCRS); also elsewhere on the board
MRXC: U4.124 (MRXC); also elsewhere on the board
MRXD0: U4.123 (MRXD[0]); also elsewhere on the board
MRXD1: U4.122 (MRXD[1]); also elsewhere on the board
MRXD2: U4.121 (MRXD[2]); also elsewhere on the board
MRXD3: U4.120 (MRXD[3]); also elsewhere on the board
MRXDV: U4.119 (MRXDV); also elsewhere on the board
MTXC: U4.102 (MTXC); also elsewhere on the board
MTXD0: U4.100 (MTXD[0]); also elsewhere on the board
MTXD1: U4.99 (MTXD[1]); also elsewhere on the board
MTXD2: U4.98 (MTXD[2]); also elsewhere on the board
MTXD3: U4.97 (MTXD[3]); also elsewhere on the board
MTXEN: U4.96 (MTXEN); also elsewhere on the board
unnamed: LED1.A, R1.1
unnamed: TP1.TP, U4.112 (LED[1][2])
unnamed: R8.2, U4.167 (MODESEL[0])
unnamed: TP2.TP, U4.113 (LED[1][1])
unnamed: R7.2, U4.166 (MODESEL[1])
unnamed: TP3.TP, U4.114 (LED[1][0])
unnamed: R6.2, U4.165 (MODESEL[2])
unnamed: Q8.3 (D), Q9.1 (G), R42.2
unnamed: LED5.A, R5.1
unnamed: TP4.TP, U4.116 (LED[2][2])
unnamed: R4.2, U4.164 (MODESEL[3])
unnamed: TP5.TP, U4.117 (LED[2][1])
unnamed: R10.1, U4.171 (CFGMODE)
unnamed: TP6.TP, U4.118 (LED[2][0])
unnamed: R2.1, U4.163 (MIIS[0])
unnamed: C12.1, D1.ANODE, Q8.1 (G), R43.1
unnamed: R13.1, U4.26 (ISET)
unnamed: LED9.A, R9.1
unnamed: TP7.TP, U4.128 (LED[3][2])
unnamed: TP8.TP, U4.129 (LED[3][1])
unnamed: R3.1, U4.170 (PRSV)
unnamed: TP9.TP, U4.130 (LED[3][0])
unnamed: LED13.A, R16.1
unnamed: TP10.TP, U4.132 (LED[4][2])
unnamed: TP11.TP, U4.133 (LED[4][1])
unnamed: TP12.TP, U4.134 (LED[4][0])
unnamed: LED17.A, R20.1
unnamed: TP13.TP, U4.138 (LED[5][2])
unnamed: TP14.TP, U4.139 (LED[5][1])
unnamed: TP15.TP, U4.140 (LED[5][0])
unnamed: LED21.A, R24.1
unnamed: TP16.TP, U4.142 (LED[6][2])
unnamed: TP17.TP, U4.143 (LED[6][1])
unnamed: TP18.TP, U4.144 (LED[6][0])
unnamed: LED25.A, R28.1
unnamed: TP19.TP, U4.146 (LED[7][2])
unnamed: TP20.TP, U4.147 (LED[7][1])
unnamed: TP21.TP, U4.149 (LED[7][0])
unnamed: R117.1, U4.109 (BIST)
unnamed: LED29.A, R32.1
unnamed: TP22.TP, U4.151 (LED[8][2])
unnamed: R116.1, U4.156 (IO_SWM)
unnamed: TP23.TP, U4.152 (LED[8][1])
unnamed: TP24.TP, U4.153 (LED[8][0])
unnamed: LED33.A, R38.1
unnamed: TP25.TP, U4.159 (LED[9][2])
unnamed: TP26.TP, U4.160 (LED[9][1])
unnamed: TP27.TP, U4.161 (LED[9][0])
unnamed: C83.1, D2.ANODE, D3.ANODE, R47.2, U4.110 (!RST)
unnamed: R118.1, U4.82 (RLPBK)
unnamed: R119.1, U4.169 (SCANEN)
unnamed: R120.1, U4.168 (TESTEN)
unnamed: LED38.A, R48.1
unnamed: R72.2, U4.101 (MTXER)
unnamed: TP40.TP, U4.87 (AUTOMDIX)
unnamed: LED38.C, Q10.1 (D)
RX1_N: U4.197 (RXM[1]); also elsewhere on the board
RX1_P: U4.196 (RXP[1]); also elsewhere on the board
RX2_N: U4.207 (RXM[2]); also elsewhere on the board
RX2_P: U4.206 (RXP[2]); also elsewhere on the board
RX3_N: U4.6 (RXM[3]); also elsewhere on the board
RX3_P: U4.5 (RXP[3]); also elsewhere on the board
RX4_N: U4.23 (RXM[4]); also elsewhere on the board
RX4_P: U4.22 (RXP[4]); also elsewhere on the board
RX5_N: U4.31 (RXM[5]); also elsewhere on the board
RX5_P: U4.30 (RXP[5]); also elsewhere on the board
RX6_N: U4.48 (RXM[6]); also elsewhere on the board
RX6_P: U4.47 (RXP[6]); also elsewhere on the board
RX7_N: U4.55 (RXM[7]); also elsewhere on the board
RX7_P: U4.54 (RXP[7]); also elsewhere on the board
RX8_N: U4.65 (RXM[8]); also elsewhere on the board
RX8_P: U4.64 (RXP[8]); also elsewhere on the board
SPI3_MOSI: U4.92 (SDA); also elsewhere on the board
SPI3_SCK: U4.93 (SCL); also elsewhere on the board
TX1_N: U4.200 (TXM[1]); also elsewhere on the board
TX1_P: U4.199 (TXP[1]); also elsewhere on the board
TX2_N: U4.204 (TXM[2]); also elsewhere on the board
TX2_P: U4.203 (TXP[2]); also elsewhere on the board
TX3_N: U4.10 (TXM[3]); also elsewhere on the board
TX3_P: U4.9 (TXP[3]); also elsewhere on the board
TX4_N: U4.20 (TXM[4]); also elsewhere on the board
TX4_P: U4.19 (TXP[4]); also elsewhere on the board
TX5_N: U4.34 (TXM[5]); also elsewhere on the board
TX5_P: U4.33 (TXP[5]); also elsewhere on the board
TX6_N: U4.44 (TXM[6]); also elsewhere on the board
TX6_P: U4.43 (TXP[6]); also elsewhere on the board
TX7_N: U4.58 (TXM[7]); also elsewhere on the board
TX7_P: U4.57 (TXP[7]); also elsewhere on the board
TX8_N: U4.62 (TXM[8]); also elsewhere on the board
TX8_P: U4.61 (TXP[8]); also elsewhere on the board
VDDIO_IN: C13.2, C14.2, C15.2, C77.2, Q9.3 (D), U4.105 (VDD-IO), U4.125 (VDD-IO1), U4.148 (VDD-IO2)

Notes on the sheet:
Ethernet Start-Up
Ethernet Reset
Mode Select

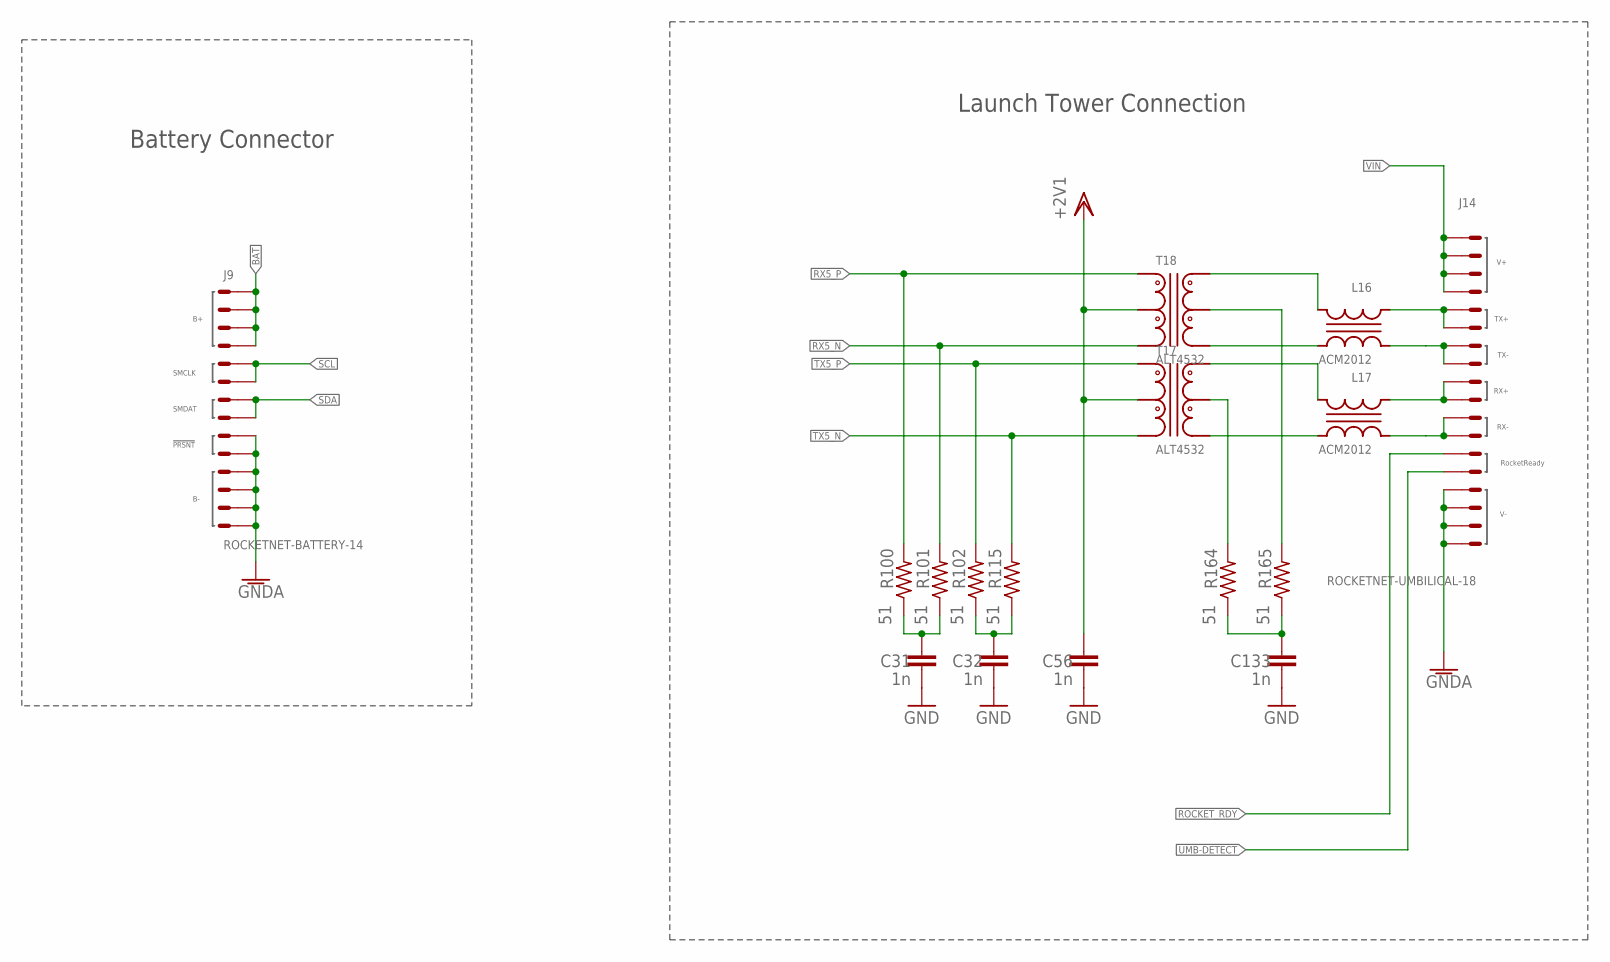
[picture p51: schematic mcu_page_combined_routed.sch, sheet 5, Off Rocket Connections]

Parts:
C31, C32, C56, C133: 1n; 0402-B-NOSILK
J9: ROCKETNET-BATTERY-14; ROCKETNET-M-14
J14: ROCKETNET-UMBILICAL-18; ROCKETNET-M-18
L16, L17: ACM2012; TDK-ACM2012
R100, R101, R102, R115, R164, R165: 51; 0402-B-NOSILK
T17, T18: ALT4532; TDK-ALT4532

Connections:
!UMB-DETECT: J14.RR@10 (RR); also elsewhere on the board
+2V1: C56.2, T17.6, T18.6; also elsewhere on the board
BAT: J9.B+@1 (B+), J9.B+@2 (B+), J9.B+@3 (B+), J9.B+@4 (B+); also elsewhere on the board
GND: C31.1, C32.1, C56.1, C133.1; also elsewhere on the board
GNDA: J9.!PRSNT@9 (!PRSNT), J9.!PRSNT@10 (!PRSNT), J9.B-@11 (B-), J9.B-@12 (B-), J9.B-@13 (B-), J9.B-@14 (B-), J14.V-@2 (V-), J14.V-@4 (V-), J14.V-@6 (V-), J14.V-@8 (V-); also elsewhere on the board
unnamed: J14.T-@11 (T-), J14.T-@13 (T-), L16.2
unnamed: L16.3, T18.4
unnamed: L17.3, T17.4
unnamed: J14.R+@5 (R+), J14.R+@7 (R+), L17.1
unnamed: C32.2, R102.1, R115.1
unnamed: J14.R-@1 (R-), J14.R-@3 (R-), L17.2
unnamed: L16.4, T18.5
unnamed: L17.4, T17.5
unnamed: R164.2, T17.3
unnamed: R165.2, T18.3
unnamed: C133.2, R164.1, R165.1
unnamed: C31.2, R100.1, R101.1
unnamed: J14.T+@15 (T+), J14.T+@17 (T+), L16.1
ROCKET_RDY: J14.RR@9 (RR); also elsewhere on the board
RX5_N: R101.2, T18.2; also elsewhere on the board
RX5_P: R100.2, T18.1; also elsewhere on the board
SCL: J9.SMCLK@3 (SMCLK), J9.SMCLK@4 (SMCLK); also elsewhere on the board
SDA: J9.SMDAT@7 (SMDAT), J9.SMDAT@8 (SMDAT); also elsewhere on the board
TX5_N: R115.2, T17.2; also elsewhere on the board
TX5_P: R102.2, T17.1; also elsewhere on the board
VIN: J14.V+@12 (V+), J14.V+@14 (V+), J14.V+@16 (V+), J14.V+@18 (V+); also elsewhere on the board

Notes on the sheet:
Launch Tower Connection
Battery Connector

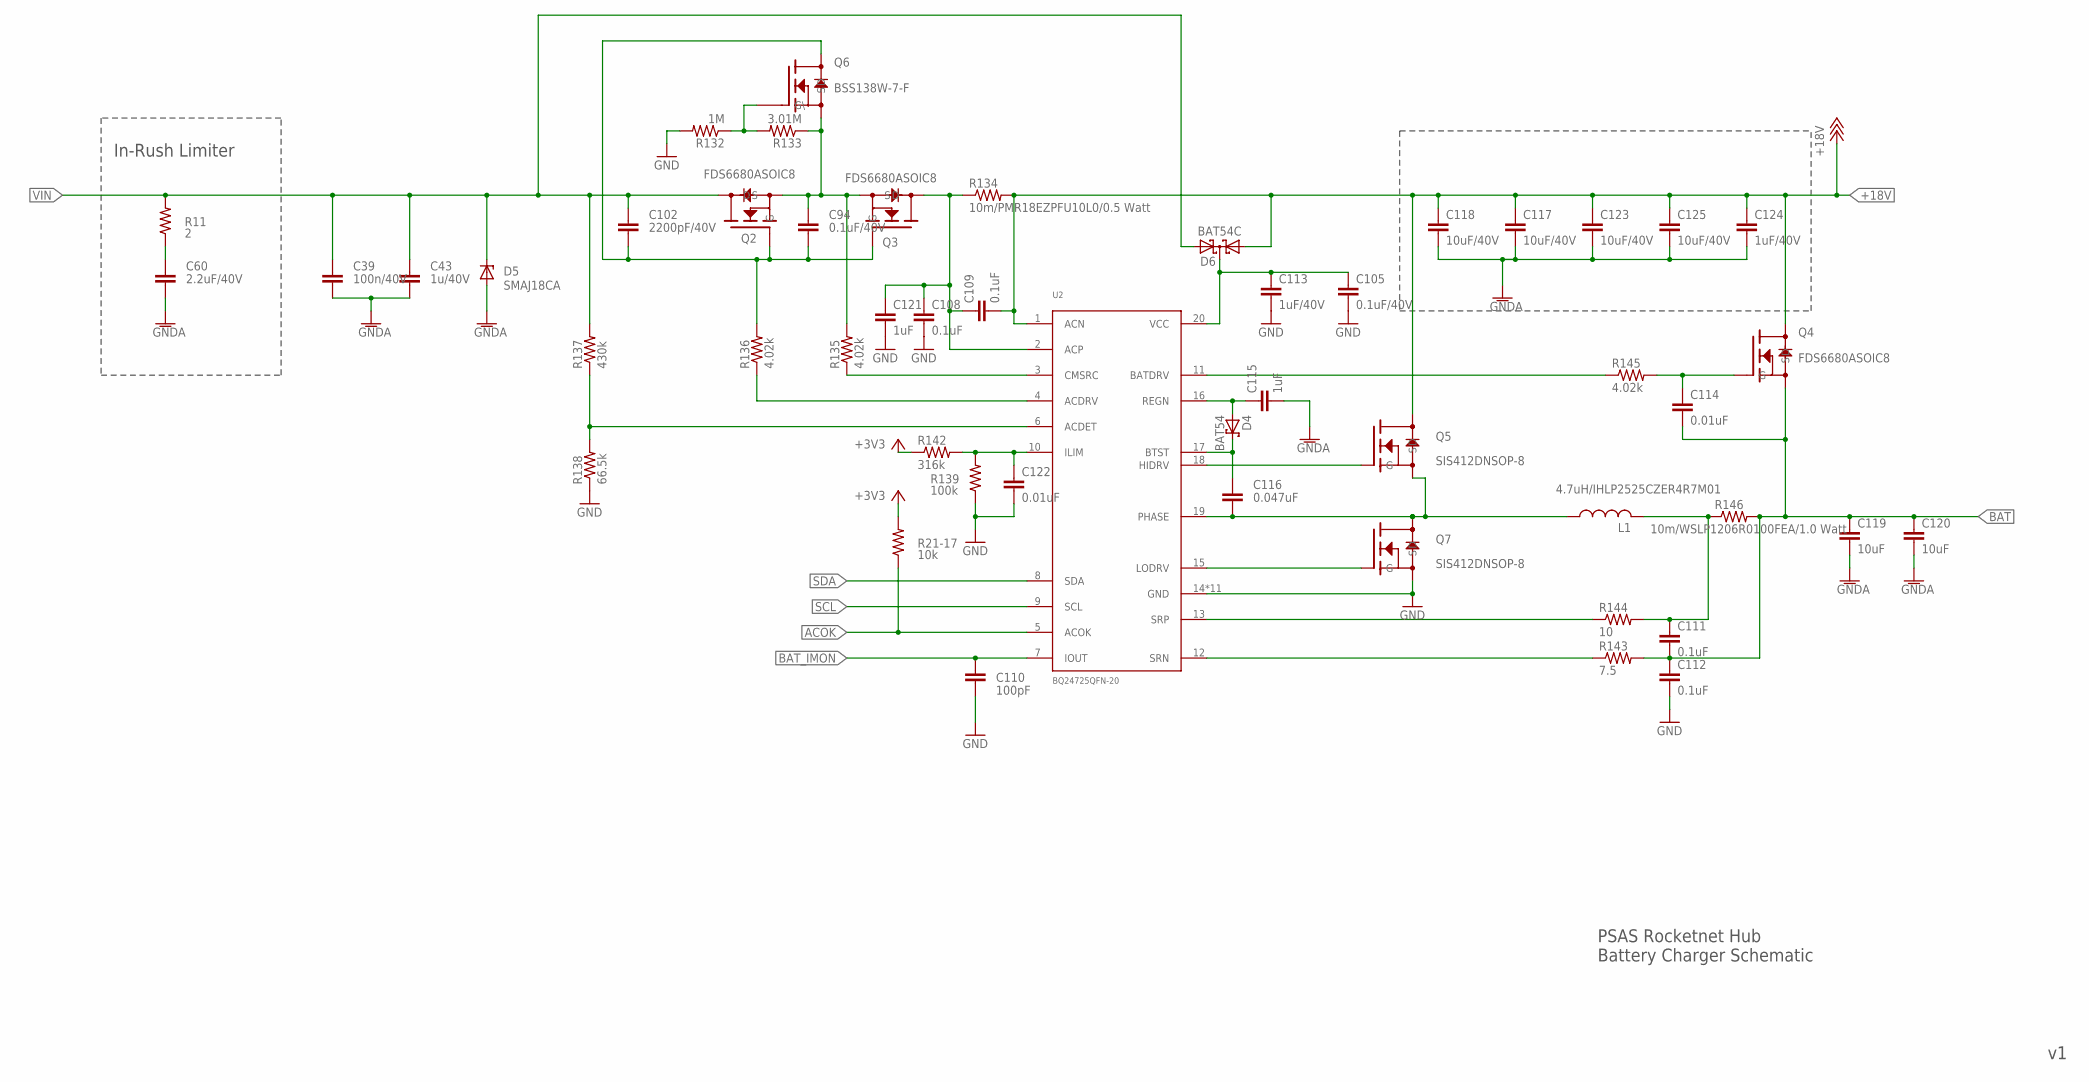
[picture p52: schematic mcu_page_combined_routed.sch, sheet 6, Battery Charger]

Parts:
C39: 100n/40V; 0402-B-NOSILK
C43: 1u/40V; 0603-B-NOSILK
C60: 2.2uF/40V; 0805-B-NOSILK
C94, C105: 0.1uF/40V; 0402-B-NOSILK
C102: 2200pF/40V; 0402-B-NOSILK
C108, C109, C111, C112: 0.1uF; 0402-B-NOSILK
C110: 100pF; 0402-B-NOSILK
C113, C124: 1uF/40V; 0603-B-NOSILK
C114, C122: 0.01uF; 0402-B-NOSILK
C115, C121: 1uF; 0603-B-NOSILK
C116: 0.047uF; 0402-B-NOSILK
C117, C118, C123, C125: 10uF/40V; 1206-B
C119, C120: 10uF; 1206-B
D4: BAT54; SOT23
D5: SMAJ18CA; D0-214AC
D6: BAT54C; SOT23
L1: 4.7uH/IHLP2525CZER4R7M01; 2525
Q2, Q3, Q4: FDS6680ASOIC8; SOIC8
Q5, Q7: SIS412DNSOP-8; 1212-8
Q6: BSS138W-7-F; SOT323
R11: 2; R2512
R21-17: 10k; 0402-B-NOSILK
R132: 1M; 0402-B-NOSILK
R133: 3.01M; 0402-B-NOSILK
R134: 10m/PMR18EZPFU10L0/0.5 Watt; 1206-B
R135, R136, R145: 4.02k; 0402-B-NOSILK
R137: 430k; 0402-B-NOSILK
R138: 66.5k; 0402-B-NOSILK
R139: 100k; 0402-B-NOSILK
R142: 316k; 0402-B-NOSILK
R143: 7.5; 0402-B-NOSILK
R144: 10; 0402-B-NOSILK
R146: 10m/WSLP1206R0100FEA/1.0 Watt; 1206-B
U2: BQ24725QFN-20; S-PVQFN-N20

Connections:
+3V3: R21-17.2, R142.1; also elsewhere on the board
+18V: C109.2, C117.1, C118.1, C123.1, C124.1, C125.1, D6.1 (A1), Q4.5 (D), Q4.6 (D), Q4.7 (D), Q4.8 (D), Q5.5 (D), Q5.6 (D), Q5.7 (D), Q5.8 (D), Q5.9 (D), R134.2, U2.1 (ACN); also elsewhere on the board
ACOK: R21-17.1, U2.5 (ACOK); also elsewhere on the board
BAT: C111.2, C112.1, C114.2, C119.1, C120.1, Q4.1 (S), Q4.2 (S), Q4.3 (S), R143.2, R146.2; also elsewhere on the board
BAT_IMON: C110.1, U2.7 (IOUT); also elsewhere on the board
GND: C105.2, C108.2, C110.2, C112.2, C113.2, C121.2, C122.2, Q7.1 (S), Q7.2 (S), Q7.3 (S), R132.2, R138.1, R139.1, U2.14 (GND), U2.P$1 (GND), U2.P$2 (GND), U2.P$3 (GND), U2.P$4 (GND), U2.P$5 (GND), U2.P$6 (GND), U2.P$7 (GND), U2.P$8 (GND), U2.P$9 (GND), U2.POWERPAD (GND); also elsewhere on the board
GNDA: C39.2, C43.2, C60.2, C115.2, C117.2, C118.2, C119.2, C120.2, C123.2, C124.2, C125.2, D5.P$1 (A); also elsewhere on the board
unnamed: C105.1, C113.1, D6.3 (CC), U2.20 (VCC)
unnamed: C94.1, Q2.1 (S), Q2.2 (S), Q2.3 (S), Q3.1 (S), Q3.2 (S), Q3.3 (S), Q6.3 (S), R133.1, R135.2
unnamed: Q6.2 (G\), R132.1, R133.2
unnamed: C94.2, C102.2, Q2.4 (G), Q3.4 (G), Q6.1 (D), R136.2
unnamed: C60.1, R11.1
unnamed: C108.1, C109.1, C121.1, Q3.5 (D), Q3.6 (D), Q3.7 (D), Q3.8 (D), R134.1, U2.2 (ACP)
unnamed: R135.1, U2.3 (CMSRC)
unnamed: R136.1, U2.4 (ACDRV)
unnamed: R137.1, R138.2, U2.6 (ACDET)
unnamed: C122.1, R139.2, R142.2, U2.10 (ILIM)
unnamed: R144.1, U2.13 (SRP)
unnamed: R143.1, U2.12 (SRN)
unnamed: C111.1, L1.P$1, R144.2, R146.1
unnamed: R145.1, U2.11 (BATDRV)
unnamed: C114.1, Q4.4 (G), R145.2
unnamed: C115.1, D4.1 (A), U2.16 (REGN)
unnamed: C116.1, D4.3 (C), U2.17 (BTST)
unnamed: Q7.4 (G), U2.15 (LODRV)
unnamed: C116.2, L1.P$2, Q5.1 (S), Q5.2 (S), Q5.3 (S), Q7.5 (D), Q7.6 (D), Q7.7 (D), Q7.8 (D), Q7.9 (D), U2.19 (PHASE)
unnamed: Q5.4 (G), U2.18 (HIDRV)
SCL: U2.9 (SCL); also elsewhere on the board
SDA: U2.8 (SDA); also elsewhere on the board
VIN: C39.1, C43.1, C102.1, D5.P$2 (C), D6.2 (A2), Q2.5 (D), Q2.6 (D), Q2.7 (D), Q2.8 (D), R11.2, R137.2; also elsewhere on the board

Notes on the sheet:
PSAS Rocketnet Hub Battery Charger Schematic
In-Rush Limiter

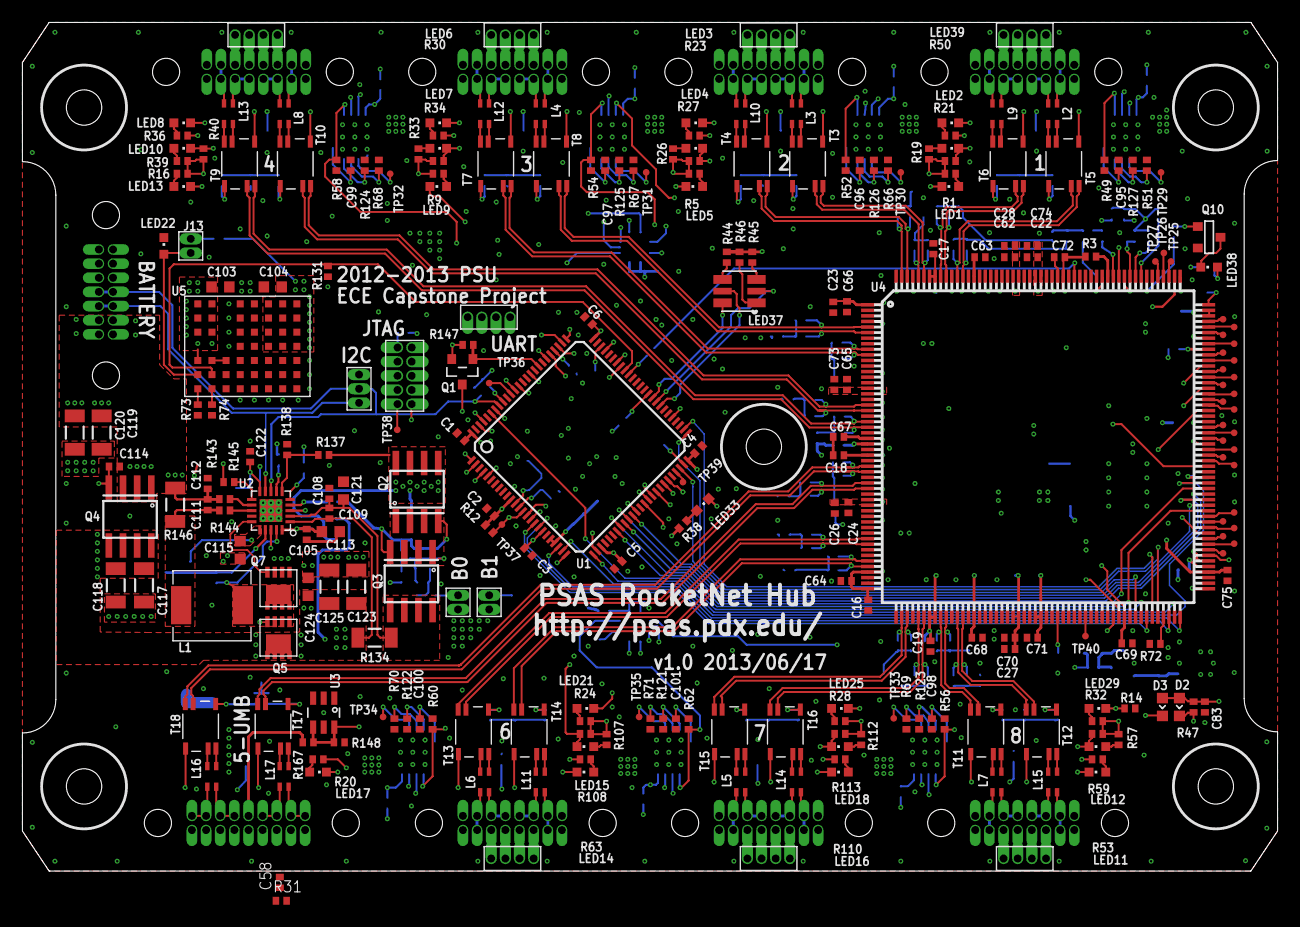
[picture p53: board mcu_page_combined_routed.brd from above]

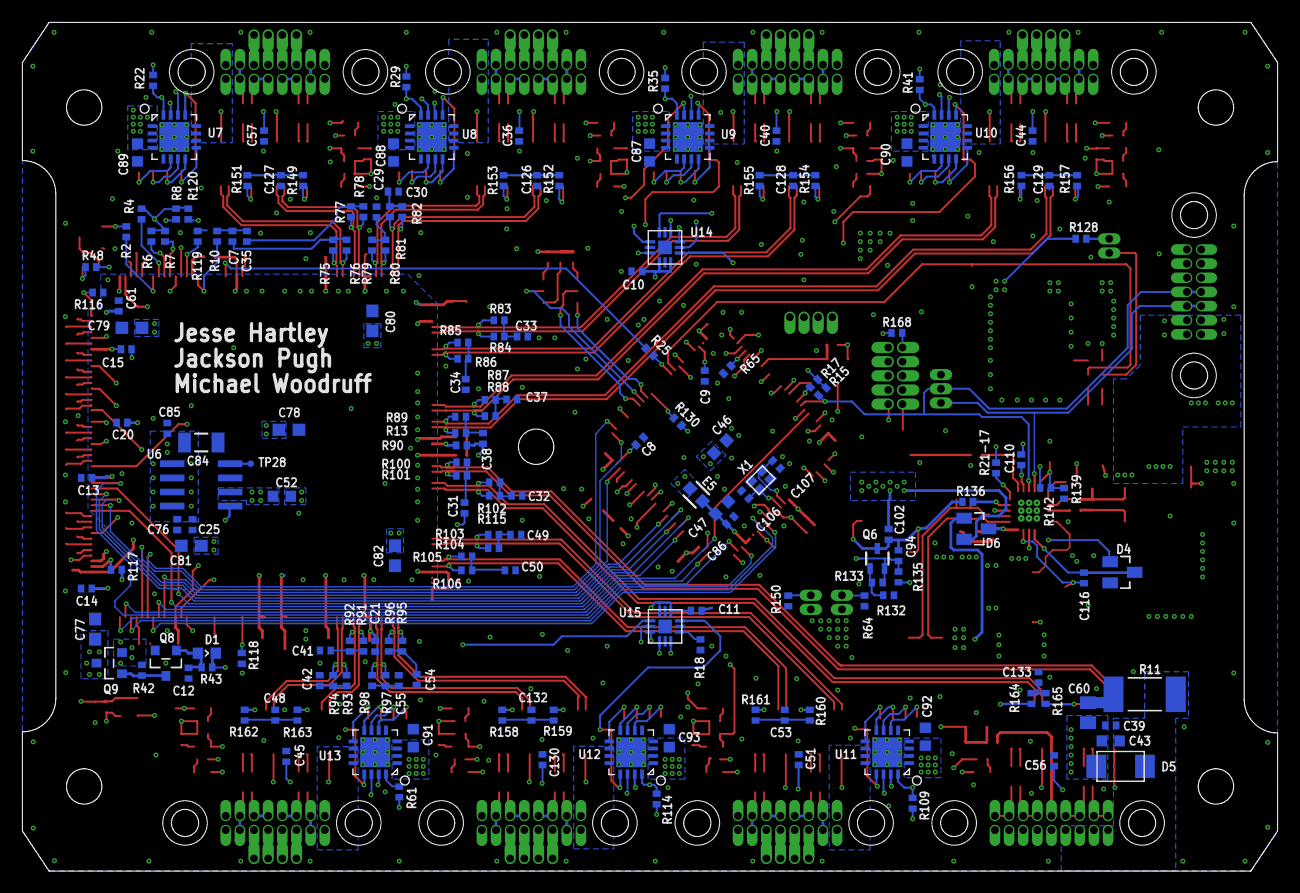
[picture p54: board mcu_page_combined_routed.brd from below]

Board: 6 copper layers, 112.7 x 76.2 mm, 451 parts (181 on the bottom side), 399 nets.

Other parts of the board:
U$1, U$21, U$22, U$23, U$24: #4-BARE_MOUNTING_HOLE/.300; #4/.300-BARE+STD_NUT_OR_STAR_WASHER

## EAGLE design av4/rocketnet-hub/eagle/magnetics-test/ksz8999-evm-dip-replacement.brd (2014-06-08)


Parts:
L1, L2: ACM2012; TDK-ACM2012
T1, T2: ALT4532; TDK-ALT4532
TP1, TP2, TP3, TP4, TP6, TP7, TP8, TP9, TP10, TP11: TEST-PAD

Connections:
unnamed: L1.3, T1.4
unnamed: L2.4, T2.5
unnamed: T2.1, TP3.P$1
unnamed: T1.6, T2.6, TP2.P$1
unnamed: L1.4, T1.5
unnamed: T2.2, TP1.P$1
unnamed: T1.2, TP4.P$1
unnamed: T1.1, TP6.P$1
unnamed: L1.2, TP10.P$1
unnamed: L1.1, TP11.P$1
unnamed: L2.1, TP8.P$1
unnamed: L2.3, T2.4
unnamed: L2.2, TP7.P$1
unnamed: T1.3, T2.3, TP9.P$1

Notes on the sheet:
RD+
RD-


Board: 2 copper layers, 12.5 x 15.5 mm, 14 parts (0 on the bottom side), 14 nets.

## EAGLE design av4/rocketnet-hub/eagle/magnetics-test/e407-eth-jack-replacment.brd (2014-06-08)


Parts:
C1: 100n; 0603-B-NOSILK
CON1: RJLBC-060TC1
L1, L2: ACM2012; TDK-ACM2012
R1, R4: 75; 0603-B-NOSILK
T1, T2: ALT4532; TDK-ALT4532
TP1: TPPAD1-13; P1-13
X3, X7: SSW-103-02-S-D
X5, X6: SSW-104-02-S-S

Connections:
unnamed: L1.3, T1.4
unnamed: L2.4, T2.5
unnamed: L2.1, X5.1
unnamed: C1.1, R1.2, R4.2
unnamed: L1.4, T1.5
unnamed: CON1.8 (RD-), X3.4
unnamed: T1.2, X3.1, X3.6
unnamed: T1.1, X3.2, X3.5
unnamed: CON1.7 (RD+), X3.3
unnamed: CON1.1 (TD+), X7.3
unnamed: T2.1, X7.2, X7.5
unnamed: L2.3, T2.4
unnamed: L1.2, X6.3
unnamed: L2.2, X6.1
unnamed: C1.2, TP1.TP
unnamed: CON1.2 (TD-), X7.4
unnamed: R4.1, T2.3
unnamed: L1.1, X5.2
unnamed: R1.1, T1.3
unnamed: CON1.3 (COM), T1.6, T2.6
unnamed: T2.2, X7.1, X7.6

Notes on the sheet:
E407 connector
Off-board connector
RD+
RD-


Board: 2 copper layers, 48.8 x 19.8 mm, 13 parts (0 on the bottom side), 21 nets.

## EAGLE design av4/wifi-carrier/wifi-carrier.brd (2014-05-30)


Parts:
BOLT, BOLT1, BOLT2, BOLT3: _4-BARE_MOUNTING_HOLE/.325; _4/.325-BARE+SMALL_TOOL_CLEARANCE
C1, C2: 100n; C0603
C3: 1u; C0805
C4: 33u; C1206
C5: 100u; 7660
CTRL: PTR1PAD1-13; P1-13
J1: ROCKETNET-CONNECTOR-16M; ROCKETNET-M-16
J2: 5V; 2POL254
R1, R2: NP; R0603
U1: UEI15; UEI15_PIN
UWIFI: ZCN-722M
VBATT: PTR1PAD1-13; P1-13
VUSB: PTR1PAD1-13; P1-13

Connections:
CTRL: CTRL.TP, U1.6 (CTRL)
D+: J1.T-@9 (TX-), J1.T-@11 (TX-), UWIFI.4 (D+)
D-: J1.R+@5 (RX+), J1.R+@7 (RX+), UWIFI.3 (D-)
GND: C1.2, C2.2, C3.2, C4.2, C5.-, J1.B-@1 (B-), J1.B-@2 (B-), J2.2, R2.1, U1.2 (INGND), U1.5 (OUTGND)
TRIM: R1.1, R2.2, U1.4 (TRIM)
USB+: J1.T+@13 (TX+), J1.T+@14 (TX+), UWIFI.2 (VCC), VUSB.TP
USB-: J1.R-@3 (RX-), J1.R-@4 (RX-), UWIFI.5 (GND)
VCC: C1.1, C5.+, J1.B+@15 (B+), J1.B+@16 (B+), U1.1 (VIN), VBATT.TP
VOUT: C2.1, C3.1, C4.1, J2.1, R1.2, U1.3 (VOUT)

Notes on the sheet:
TO PA


Board: 2 copper layers, 68.6 x 67.3 mm, 18 parts (0 on the bottom side), 9 nets.

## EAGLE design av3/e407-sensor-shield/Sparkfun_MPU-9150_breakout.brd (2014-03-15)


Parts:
C1, C4: 0.1uF; 0402-CAP
C2: 2.2nF; 0402-CAP
C3: 10nF; 0402-CAP
JP1: M11PTH; 1X11
JP2, JP3: STAND-OFF
JP4: LOGO-SFENW2; SFE-NEW-WEB
JP6: LOGO-SFESK; SFE-LOGO-FLAME
JP7, JP8: FIDUCIALUFIDUCIAL; MICRO-FIDUCIAL
R1, R2: 10k; 0402-RES
SJ1: SOLDERJUMPER_2WAYPASTE2&3; SJ_3_PASTE2&3
SJ2**, SJ3**: SOLDERJUMPERTRACE; SJ_2S-TRACE
U1: MPU-9150; QFN-24-NP
U$1: OSHW-LOGOS; OSHW-LOGO-S

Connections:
AD0: JP1.3, SJ1.2, U1.9 (AD0)
CLKIN: JP1.4, SJ2**.2, U1.1 (CLKIN)
CLKOUT: JP1.5, U1.22 (CLKOUT)
ESC: JP1.6, U1.7 (E_SCL)
ESD: JP1.7, U1.6 (E_SDA)
FSYNC: JP1.2, SJ3**.2, U1.11 (FSYNC)
GND: C1.2, C2.2, C3.2, C4.2, JP1.11, SJ1.3, SJ2**.1, SJ3**.1, U1.15 (GND), U1.17 (GND), U1.18 (GND)
INT: JP1.1, U1.12 (INT)
unnamed: C2.1, U1.20 (CPOUT)
unnamed: C4.1, U1.10 (REGOUT)
SCL: JP1.8, R2.1, U1.23 (SCL)
SDA: JP1.9, R1.1, U1.24 (SDA)
VCC: C1.1, C3.1, JP1.10, R1.2, R2.2, SJ1.1, U1.3 (VDD), U1.8 (VLOGIC), U1.13 (VDD)

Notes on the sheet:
50V
I2C Address Selection
**Optional external reference clock input or synchornization digital input.
Connected to GND by default. Cut trace for external control
Default Address = 0x68 (pin AD0 is logic low)
Alternative Address =0x69 (pin AD0 is logic high)
*The LSB bit of the 7 bit address is determined by the logic level on pin AD0.
default to GND
A. Weiss
*2.375V < VCC < 3.465V



Board: 2 copper layers, 15.2 x 27.9 mm, 19 parts (5 on the bottom side), 13 nets.

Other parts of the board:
JP5: LOGO-SFESK; SFE-LOGO-FLAME

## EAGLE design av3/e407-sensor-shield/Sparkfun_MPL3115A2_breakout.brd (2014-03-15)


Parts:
C1, C3: 0.1uF; 0402-CAP
C2: 10uF; EIA3216
C4: 1uF; 0402-CAP
JP1, JP5: LOGO-SFESK; SFE-LOGO-FLAME
JP2, JP3: STAND-OFF
JP4: M06SIP; 1X06
JP6, JP7: FIDUCIALUFIDUCIAL; MICRO-FIDUCIAL
R1, R2: 1k; 0402-RES
U1: MPL3115A2LGA8; LGA8
U$1: OSHW-LOGOS; OSHW-LOGO-S
U$2: CREATIVE_COMMONS

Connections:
GND: C1.2, C2.C (-), C3.2, C4.2, JP4.6, U1.3 (GND)
INT1: JP4.2, U1.6 (INT1)
INT2: JP4.1, U1.5 (INT2)
unnamed: C3.1, U1.2 (CAP)
SCL: JP4.4, R1.1, U1.8 (SCL)
SDA: JP4.3, R2.1, U1.7 (SDA)
VCC: C1.1, C2.A (+), C4.1, JP4.5, R1.2, R2.2, U1.1 (VDD), U1.4 (VDDIO)

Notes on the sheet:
A.Weiss
VCC = 3.6V Max
Read Address:
Write Address:
Slave Address:
0x60
0xC1
0xC0



Board: 2 copper layers, 15.2 x 17.8 mm, 16 parts (2 on the bottom side), 7 nets.

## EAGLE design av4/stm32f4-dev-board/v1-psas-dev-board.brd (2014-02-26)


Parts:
C10, C62: 100n 10V; 0402-C-NOSILK
C20: 2.2u 10V; 0603-C-NOSILK
C29, C30: 18pF 10V; 0402-C-NOSILK
C45, C46, C47, C48, C49, C50: 100nF 10V; 0402-C-NOSILK
C51, C52: 2.2uF 10V; 0603-C-NOSILK
J1: 1.27MM-SWD-CONNECTOR; 1.27MM_2X5
LED2: BLUE; CHIP-LED0603
LED3: GREEN; CHIP-LED0603
LED4: RED; CHIP-LED0603
Q1: NTR4101P; SOT23
R12: 1.5k; 0402-C-NOSILK
R18: 10k; 0402-C-NOSILK
R38, R39: 68; 0402-C-NOSILK
R40: 27; 0402-C-NOSILK
SD1: CON_HIROSE_DM3D(MICROSD); HIROSE_DM3D(MICRO-SD)
TP1: TPTP06R; TP06R
U8: STM32F4V; LQFP100
USB: ZX62D-B-5P8
X1: 25 MHz; CTS406

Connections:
3.3VD: C45.2, C46.2, C47.2, C48.2, C49.2, C50.2, C51.2, C52.2, J1.VTREF, Q1.2 (S), R12.2, R18.2, R38.1, R39.1, R40.1, U8.VCAP1 (VCAP_1), U8.VCAP2 (VCAP_2), U8.VDD1, U8.VDD2, U8.VDD3, U8.VDD4, U8.VDD5, U8.VDD6; also elsewhere on the board
!RST: J1.!RESET, R18.1, U8.NRST
EPHY_NRST: U8.PA1; also elsewhere on the board
ETH_CRX_DV: U8.PA7; also elsewhere on the board
ETH_MDC: U8.PC1; also elsewhere on the board
ETH_MDINT: U8.PA3; also elsewhere on the board
ETH_MDIO: U8.PA2; also elsewhere on the board
ETH_RXD0: U8.PC4; also elsewhere on the board
ETH_RXD1: U8.PC5; also elsewhere on the board
ETH_TXD0: U8.PB12; also elsewhere on the board
ETH_TXD1: U8.PB13; also elsewhere on the board
ETH_TX_EN: U8.PB11; also elsewhere on the board
GND: C10.1, C20.1, C29.1, C30.1, C45.1, C46.1, C47.1, C48.1, C49.1, C50.1, C51.1, C52.1, C62.1, J1.GND, J1.GND@2 (GND), J1.GNDDET, SD1.G1 (PAD), SD1.G2 (PAD), SD1.G3 (PAD), SD1.G4 (PAD), SD1.P6 (6), SD1.S0 (0), SD1.S1 (1), U8.PDR_ON, U8.VSS1, U8.VSS2, U8.VSS3, USB.P5 (GND); also elsewhere on the board
LED2: LED2.C, U8.PD11
LED3: LED3.C, U8.PD13
LED4: LED4.C, U8.PD14
unnamed: LED4.A, R39.2
unnamed: LED3.A, R38.2
unnamed: LED2.A, R40.2
unnamed: TP1.TP, U8.BOOT0
OSC_IN: C30.2, U8.PH0, X1.3 (2)
OSC_OUT: C29.2, U8.PH1, X1.1
OTG_FS_DM: U8.PA11, USB.P2 (D-)
OTG_FS_DP: U8.PA12, USB.P3 (D+)
OTG_FS_VBUS: U8.PA9, USB.P1 (VCC); also elsewhere on the board
PE0: Q1.1 (G), R12.1, U8.PE0
PHY_CLK_25MHZ: U8.PA8; also elsewhere on the board
SDIO_CLK: SD1.P5 (5), U8.PC12
SDIO_CMD: SD1.P3 (3), U8.PD2
SDIO_D0: SD1.P7 (7), U8.PC8
SDIO_D1: SD1.P8 (8), U8.PC9
SDIO_D2: SD1.P1 (1), U8.PC10
SDIO_D3: SD1.P2 (2), U8.PC11
SHLD: C62.2, USB.P$1 (SHLD), USB.P$2 (SHLD), USB.P$3 (SHLD), USB.P$4 (SHLD)
TCK: J1.SWDCLK (SWDCLK/TCK), U8.PA14
TDI: J1.NC (NC/TDI), U8.PA15
TDO: J1.SWO (SWO/TDO), U8.PB3
TMS: J1.SWDIO (SWDIO/TMS), U8.PA13
VDD: C10.2, C20.2, Q1.3 (D), SD1.P4 (4)

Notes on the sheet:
MICROSD


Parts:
C1: 1uF 50V; 0805-B-NOSILK
C21: 220nF 10V; 0402-C-NOSILK
C25, C54: 100n; 0402-B-NOSILK
C26: 220nF; 0402-C-NOSILK
C33: 10uF 50V; 1206-C
C38: 100u; EIA6032
C39: 1uF; 0603-B-NOSILK
D2: DIODE-0603; 0603-B-NOSILK-DIODE
LED1: GREEN; CHIP-LED0603
R1: 10k; 0402-C-NOSILK
R3: 3.3k; 0402-C-NOSILK
R6: 68; 0402-C-NOSILK
R7: 249k; 0402-C-NOSILK
U10: LMZ12001; TO-PMOD-7
U$1, U$12, U$14, U$18: #4-BARE_MOUNTING_HOLE/.300; #4/.300-BARE+STD_NUT_OR_STAR_WASHER

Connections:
3.3VD: C26.1, C38.P$1 (+), C39.1, C54.1, LED1.A, R1.2, U10.7 (VOUT); also elsewhere on the board
GND: C1.2, C21.2, C25.2, C33.2, C38.P$2 (-), C39.2, C54.2, R3.1, R6.1, U10.4 (GND), U10.EP; also elsewhere on the board
unnamed: C21.1, U10.5 (SS)
unnamed: C26.2, R1.1, R3.2, U10.6 (FB)
unnamed: R7.2, U10.2 (RON)
unnamed: LED1.C, R6.2
OTG_FS_VBUS: D2.ANODE; also elsewhere on the board
VIN: C1.1, C25.1, C33.1, D2.CATHODE, R7.1, U10.1 (VIN); also elsewhere on the board

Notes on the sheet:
4.5 - 26 Vin
Vsys to 3.3V
Aux supply from USB debug
1206
0805


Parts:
C23, C27, C28: 22uF/6.3V; 1206-C
C31, C32, C34, C35, C37, C53: 100nF 10V; 0402-C-NOSILK
C36: 10uF/6.3V; 1206-C
C44: 1nF 10V; 0402-C-NOSILK
J3: ROCKETNET-CONNECTOR-16M; ROCKETNET-M-16
L1, L4: ACM2012; TDK-ACM2012
L3: FB0805/600R/200mA(201209-601); 0805-C-NOSILK
R10, R11: 75; 0402-C-NOSILK
R15: 150; 0402-C-NOSILK
R16: 2.2k; 0402-C-NOSILK
R20: 0R; 0402-C-NOSILK
R22, R23, R24, R25: 49.9R/1%; 0402-C-NOSILK
R27, R42, R43, R44, R45, R46, R47, R48: 4.7k; 0402-C-NOSILK
R28: 10k; 0402-C-NOSILK
R29: 12.1k/1%; 0402-C-NOSILK
T1, T2: ALT4532; TDK-ALT4532
TP22, TP26, TP32, TP33: TEST-POINT; 2MM-TEST-POINT
U3: LAN8710A-EZC; QFN-32(DRILLS)

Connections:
3.3VD: C27.2, C28.2, C35.1, L3.2, R16.1, R27.1, R28.1, R42.1, R43.1, R44.1, R45.1, U3.12 (VDDIO); also elsewhere on the board
AUX1: J3.A1 (AUX1), TP22.1
AUX2: J3.A2 (AUX2), TP26.1
AUX3: J3.A3 (AUX3), TP32.1
AUX4: J3.A4 (AUX4), TP33.1
EPHY_NRST: C36.2, R28.2, U3.19 (NRST); also elsewhere on the board
ETH_CRX_DV: R45.2, U3.15 (COL/CRS_DV/MODE2); also elsewhere on the board
ETH_MDC: U3.17 (MDC); also elsewhere on the board
ETH_MDINT: R15.1, R16.2; also elsewhere on the board
ETH_MDIO: R44.2, U3.16 (MDIO); also elsewhere on the board
ETH_RXD0: R42.2, U3.11 (RXD0/MODE0); also elsewhere on the board
ETH_RXD1: R43.2, U3.10 (RXD1/MODE1); also elsewhere on the board
ETH_TXD0: U3.22 (TXD0); also elsewhere on the board
ETH_TXD1: U3.23 (TXD1); also elsewhere on the board
ETH_TX_EN: U3.21 (TXEN); also elsewhere on the board
GND: C23.1, C27.1, C28.1, C31.1, C32.1, C34.1, C35.2, C36.1, C37.1, C44.1, C53.1, J3.B-@1 (B-), J3.B-@2 (B-), R29.1, R46.2, R47.2, R48.2, U3.24 (TXD2), U3.25 (TXD3), U3.GND; also elsewhere on the board
unnamed: J3.T+@13 (TX+), J3.T+@14 (TX+), L1.1
unnamed: C44.2, R10.1, R11.1
unnamed: J3.T-@9 (TX-), J3.T-@11 (TX-), L1.2
unnamed: J3.R+@5 (RX+), J3.R+@7 (RX+), L4.1
unnamed: J3.R-@3 (RX-), J3.R-@4 (RX-), L4.2
unnamed: L1.4, T1.1
unnamed: L1.3, T1.2
unnamed: L4.4, T2.1
unnamed: L4.3, T2.2
unnamed: R11.2, T1.6
unnamed: R10.2, T2.6
unnamed: R22.1, T2.4, U3.30 (RXN)
unnamed: R25.1, T1.5, U3.29 (TXP)
unnamed: R24.1, T1.4, U3.28 (TXN)
unnamed: R23.1, T2.5, U3.31 (RXP)
unnamed: R29.2, U3.32 (RBIAS)
unnamed: C37.2, R20.1, T1.3, T2.3
unnamed: C34.2, C53.2, U3.6 (VDDCR)
unnamed: R15.2, U3.18 (NINT/TXER/TXD4)
PHYAD0: R46.1, U3.13 (RXER/RXD4/PHYAD0)
PHYAD1: R47.1, U3.7 (RXCLK/PHYAD1)
PHYAD2: R48.1, U3.8 (RXD3/PHYAD2)
PHY_CLK_25MHZ: U3.5 (XTAL1/CLKIN); also elsewhere on the board
RMIISEL: R27.2, U3.9 (RXD2/RMIISEL)
VDDA: C23.2, C31.2, C32.2, L3.1, R20.2, R22.2, R23.2, R24.2, R25.2, U3.1 (VDD2A), U3.27 (VDD1A)
VIN: J3.B+@15 (B+), J3.B+@16 (B+); also elsewhere on the board

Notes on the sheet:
ETHERNET PHY
Common Mode Filters
Pulse Transformers


Board: 4 copper layers, 65.8 x 43.9 mm, 88 parts (0 on the bottom side), 72 nets.

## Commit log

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2004-10-21 Added LV1 PCBs. Note these files don't have schematic (.sch) files; they're board layouts only.
    [lv1-fc-1.brd, lv1-imu-accel-1.brd, lv1-imu-array-1.brd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]
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2004-10-21 Updated schematic (and possibly board, although that's an unknown) because of bugs/missing components in the board.
    [lv1b-fc-1.brd, lv1b-fc-1.sch]
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2004-10-21 Problems with the 9/9/2000 (v1.2) build of the LV1B IMU board.
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2005-08-13 v1.10 of psas library. Added parts for gpl-gps MG5001 development board. Also tried to get non-auto pad sizes for parts. Didn't work for some reason.
2006-02-15 TAB added some higher funct key repeats for right handed use, as well as board specific bindings.
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2006-03-17 Corrected mistakes in pin directions for LPC2148 symbol.
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2006-05-27 Update of node 4 after Jacob and I set all the correct packages and part numbers. G.N. LeBrasseur 26-May-2006
    [node4-frontend.brd, node4-frontend.sch]
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2006-05-29 Named SPS nets, and fixed a few names in devices including the LPC2148 in the psas library.
    G.N. LeBrasseur J.Davidson 28-May-2006
    M eagle/lv2-node4-frontend/node4-frontend.sch
    M eagle/lv2-node4-frontend/node4.lbr
    M eagle/lv2-node4-frontend/node4-frontend.brd
    M eagle/libraries/psas_eagle_library.lbr
    [node4-frontend.brd, node4-frontend.sch]
2006-06-01 Changes to resistor symbols, and fixed broken wires
    G.N.LeBrasseur J.Davidson 31-May-2006
    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
    [node4-frontend.sch]
2006-06-08 Double cross checked bus net names. Lables on bus nets, and connectors.
    Considered final version. (1.0 ?)
    G.N. LeBrasseur
    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
    [node4-frontend.sch]
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2006-06-10 Changed debug connector to correct JST part. Fixed bus wires, More detail around analog connections. Different ground symbols where ground changes. Border and text updates. Chip part numbers are comp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
    G.N. LeBrasseur 10-Jun-2006
    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
    [node4-frontend.sch]
2006-06-16 15-Jun-2006 G.N. LeBrasseur J. Davidson
    Add LT spice schematic directory
    Trivial modification to node4 schematic
    A eagle/lv2-node4-frontend/LTSpice_Schematics
    A eagle/lv2-node4-frontend/LTSpice_Schematics/SPS_rev2_2.asc
    A eagle/lv2-node4-frontend/LTSpice_Schematics/Readme.txt
    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
    [node4-frontend.brd, node4-frontend.sch]
2006-07-19 19-Jul-2006 G.N. LeBrasseur Fixed several things on schematic found wrong just before presented project. Board will now correctly ERC. Moved USB TVSS to protect RF filter Add jumper to VBAT Deleted o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
    Modifications to: eagle/lv2-node4-frontend/node4-frontend.sch
    [node4-frontend.sch]
2006-07-19 19-Jul-2006 G.N. LeBrasseur
    Replaced board layout
    Previous version destroyed (actually saved copy on my Linux box "salamander").
    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
    [node4-frontend.brd, node4-frontend.sch]
2006-07-23 22-Jul-2006 G.N. LeBrasseur Moved components near USB connector together.
    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
    [node4-frontend.brd, node4-frontend.sch]
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2009-03-16 Big reorganization of the avionics cad files, to make them board board centric.
    [aps.brd, aps.sch, aps_batt_board.brd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]
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2009-04-10 Added HAP charger and HAP regulator initial designs for review and work.
    [HAP-Charger_rev1.sch, hap-output-regulator_rev2.sch]
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2009-04-24 Updated the Node 5 front end schematic. Still a work in progress.
    [node5-frontend-rev2.sch]
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2009-04-24 commit 4/24/09 added values to thermistor, and its related parts. added created p-channel mosfets. expanded schematic to be more readable
    [APSCHARGER.sch]
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2009-04-25 Slight updates, while I fix my git setup.
    [node5-frontend-rev2.sch]
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2009-04-27 Changed the LTC4085-1 to the LTC4085 to reflect interest in 4.2V float voltage to battery from the charger. This will allow for slightly longer run time when battery power is necessary.
    [node5-frontend-rev2.sch]
2009-04-27 Added new file(sps-plus-charger.sch), potential SPS-HAP combination circuit using the LTC4090 switching buck and charger. The component values are all wrong at this point and are for circuit visualiz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
    [node5-frontend-rev2.sch, sps-plus-charger.sch]
2009-04-28 Completed some component selection for the LTC4090. Made minor cosmetic changs to the schematics.
    [node5-frontend-rev2.sch, sps-plus-charger.sch]
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2009-05-01 This is the third revision of APS power switches, USB hub, and shore power schematic. Added 5/1/09
    [APS_PowerSwitches_USBhub_rev3.sch]
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2009-05-03 More redlines done, another review shows another 25 or so things to be done. Highlighted problem areas in the guide layer. Most problems are part selection/pad_design related, some are signal connect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
    [node5-frontend.sch]
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2009-05-22 Beginnings of node5-frontend layout are here. They need lots of work. Completed several more redline repairs to the node5-frontend.sch file. Still more to do there as well. Need stuck bit rework, nee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
    [node5-frontend.brd, node5-frontend.sch]
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2009-05-24 More Layout complete. Still need to redisign the stuck bit circuit.
    [node5-frontend.brd, node5-frontend.sch]
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2010-02-25 Cleaned up errors on final schematic
    [final_schematic.sch]
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2010-03-03 Cleaned up errors
    [final_schematic.sch]
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2010-03-03 Added test points. Replaced JTAG connector with 12 pin 2mm Dual Row Single Wafer
    [final_schematic.sch]
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2010-03-05 Some ERC warnings cleaned up. Snapped some TQM LBR pins to grid. Renamed TQM name on schematic. Change by-pass capacitor values.
    [final_schematic.sch]
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2010-03-09 Cleared ERC errors. Corrected the grid.
    [final_schematic.sch]
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2010-03-09 Cleaned up schematic. Added bypass caps, corrected CAN transciever.
    [final_schematic.sch]
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2010-03-09 Cleaned up USB power switch; fixed directions and value/prefix in device.
    [final_schematic.sch]
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2010-03-10 fixed unclear labels
    [final_schematic.sch]
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2010-03-29 FLipped USB2
    [final_schematic.sch]
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2010-04-03 ERC errors cleaned
    [final_schematic.sch]
2010-04-07 Big clean up of schematic: Fixed lots of little errors (caps in wrong places, missing caps, bad R values), cleaned up two warnings, and fixed IDE connector to correctly reflect pin numbers and names.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
    [final_schematic.sch]
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2010-04-07 Cleaned errors
    [final_schematic.brd, final_schematic.sch]
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2010-04-08 Fixed IDE connector footprint.
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2010-04-15 Moved replaced resistors closer to the components. Aligned IDE resistors to the pins.
    [final_schematic.brd]
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2010-05-14 USB, CAN, LED, JTAG drc error checked.
    [final_schematic.brd, final_schematic.sch]
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2010-05-14 DRC Errors cleaned.
    [final_schematic.brd]
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2010-05-15 Cleared DRC errors on layer 2 and 3.
    [final_schematic.brd, final_schematic.sch]
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2010-05-15 TQM and Holes moved to compress board to 4 x 4.75 inches. Corrected layer 2 polygon.
    [final_schematic.brd]
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2010-05-15 Diodes CR1000 and CR1001 changed to 0603 package CDBU0520. IDE Connector - +3v3 pins re-routed. AGND on U1000 moved to eliminate DRC error. U1000 - All DRC drill dimension and drill size errors appro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
    [final_schematic.brd, final_schematic.sch]
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2010-05-17 Replaced CR1000 and CR1001 with RB751S40 Replaced Rocketbus connector. REF re-routed.
    [final_schematic.brd, final_schematic.sch]
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2010-05-17 DRC Errors cleaned on Ethernet Board.
    [Ethernet_Conboard.brd]
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2010-05-18 Ethernet Board - Replaced all resistors and capacitors with rcl_custom library components nonsilk components.
    [Ethernet_Conboard.brd, Ethernet_Conboard.sch, final_schematic.brd]
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2010-05-18 Added another cap on the clock circuit for good measure. Redid layout of clock circuit to be tighter and kill off unecessary vias. Moved layer 3 +3v3 polygon to board edges, and set +5v polygon to be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
    [final_schematic.brd, final_schematic.sch]
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2010-05-19 Removed label on tqm footprint in library. Massive re-routing of USB sections. Fixed USB topology that was for a device, not a host. Lots of rerouting around connectors.
    [final_schematic.brd, final_schematic.sch]
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2010-05-19 Ethernet jack was mistakenly mirrored on board; flipped, and dealy with consequences.
    [Ethernet_Conboard.brd]
2010-05-20 Corrections - 22uF capacitor. Part numbers filled in carrier-bom xls
    [carrier-bom.xls, final_schematic.brd, final_schematic.sch]
2010-05-20 More board cleanup: extracted many parts from the board file to separate library files and edited the libraries to reduce the number of drc errors on the drc. Changed some symbols to have better erc 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
    [final_schematic.brd, final_schematic.sch]
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2010-05-20 After doing BOM, switched "100 uF 0603" caps to actual existing caps :) Also swapped out DCU D flipflops to DCT since they exist.
    [fc-carrier.brd, fc-carrier.sch]
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2010-05-21 Updated BOM with actual part numbers. Lots of part name and value cleanup. Added more caps for noise suppression.
    [fc-carrier-bom.xls, fc-carrier.brd, fc-carrier.sch]
2010-05-21 Swapped out Q1000 with a transistor that we can actually get, despite the fact it's ginormous. Cleaned up polygons and tnames.
    [fc-carrier.brd, fc-carrier.sch]
2010-05-21 Added silk and tdoc to the SN74LS92, and fixed the placement of the standoffs - they were off by 5mm.
    [fc-carrier-bom.xls, fc-carrier.brd, fc-carrier.sch]
2010-05-23 Per Andrew's instructions, changed some IO_GND to regular GND on C6, U$8. Fixed some DRC errors, mainly traces being too close.
    [node5-frontend.brd, node5-frontend.sch]
2010-05-27 Changes to carrier board and ethernet board for manufacturing and parts procurement - switched to DPAK transitor, switched some caps to other packages, etc. BOM should be correct now. Sent carrier ou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
    [ethernet-frontend.brd, ethernet-frontend.sch, fc-carrier-bom.xls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]
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2010-05-28 Fixed DRCs, new DRU from Andrew, new schematic symbols for rocketbus connector and choke
    [node5-frontend.brd, node5-frontend.sch]
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2010-09-01 Added first draft of the FC carrier breakout board. Fixed two issues in FC carrer: moved 47K out of the path of the feedback loop (TODO: NEEDS TO BE VERIFIED THIS WILL WORK) and also fixed LED buffer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
    [breakout-board.brd, breakout-board.sch, fc-carrier.brd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]
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2010-09-23 Incremental changes to GFE - nearly done electrically
    - All parts placed
    - Itty Bitty Pads replaced with through-hole type
    - Pads placed such that all traces should be routable, and may be passed
    to "backend" or "east" portion of the board by way of the traces that
    feed the through-hole pads
    - Intermediate power is available on the "north" section by way of vias
    To Do:
    - Finish routing of all traces
    - Verify all connections relying on polygons are contacted by polygons
    - "Stitching" of ground planes
    - Useful name layout for silkscreen
    [node6.9.10-frontend.brd, node6.9.10-frontend.sch]
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2010-09-28 GFE Layout Effectively Done.
    * Needs stitching of ground plane and parts placement silk screen
    corrected.
    * Should have someone more experienced check that the power plane is
    acceptable. Power plane might need bridging.
    * Should be checked to ensure that all connections expected to be made
    via polygon are made sufficiently.
    * Also, Hooray!
    [node6.9.16-frontend.brd, node6.9.16-frontend.sch]
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2010-11-03 Fixed battery footprint - can now put leads in the middle. Finished placing components on the sensor board, so it's time to finish the schematic.
    [av3-batter-board.brd, av3-batter-board.sch]
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2010-11-24 Worked on the front end layout a bit, up to the SPS chip. Packed it in a little tighter.
    [node5-frontend.brd, node5-frontend.sch]
2010-12-02 Components placed. Needs routing. Happy Hanukkah!
    There's really not much more to say on this one, but I'd hate to
    dissapoint the diligent fellow that actually reads these notes. I will
    add that there is plenty of routing to be done, and I just may try the
    autorouter for kicks. Also, congnac and cigars make for cheerful vices.
    If I have to burn hitpoints for pleasure, man that's the way to fly!
    [node5-frontend.brd]
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2010-12-22 GFE board layout completed (draft)
    GFE board layout is effectively complete. Could almost certainly use some finishing touches. There are
    however no remaining airwires, no obvious issues, and no glaring DRC flaws.
    Enjoy!
    [node5-frontend.brd]
2010-12-22 Fixed the FC carrier board: Jumpered grounds together, Added signal names, reverted change to MAX5902 drain resistor circuit.
    [fc-carrier.brd, fc-carrier.sch]
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2011-01-20 GFE layout is done. New layout of application connections, added uart0 connection to aux pins on rocketbus connector with ESD protection, rerouted many lines to remove layer 2 and 15 wires, fixed som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
    [node5-frontend.brd, node5-frontend.sch]
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2011-01-26 OMG!!! How could I **NOT** put an RGB LED on this board... oh, the horror. Also fixed footprint of debug connector.
    [node5-frontend.brd, node5-frontend.sch]
2011-02-02 Fixed clock (switched to 1/8 speed = 1.5 MHz), changed j-cut from 1206 to 0603, replaced 0 ohms with jcuts, generic clean ups. Left to do: better part names, silk screen cleanup.
    [node5-frontend.brd, node5-frontend.sch]
2011-02-10 Lots of small changes: upgraded TVS2000 because it wasn't big enough, fixed a billion tdoc/tplace drawings on various custom packages, fixed up the top and bottom silk layers.
    [breakout-board.brd, breakout-board.sch, node5-frontend.brd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]
2011-02-21 All sorts of cleanup parts cleanup! Two caps on output of HAP, added D flip flop power off circuitry, switched crystal footprints, removed useless GPIO lines to charger, and more! To be done: silk sc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
    [node5-frontend.brd, node5-frontend.sch]
2011-02-22 Final board cleanup - fixed CAN dominant bit stuck circuit, lots of cleanup on component values, silk screen clean up, etc. Boards D-O-N-E.
    [node5-bom.xls, node5-frontend.brd, node5-frontend.sch]
2011-02-22 Gerbers or it didn't happen.
    [node5-frontend.xln]
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2011-05-08 Commit of "fixed" node5 GFE. Added xtal/sps sync level shifting circuit, switched usb pullup to correct GPIO line, moved SPS caps around a bit for better spacing, cleaned up the silk screen, and that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
    [node5-frontend.brd, node5-frontend.sch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]
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2011-06-16 ARGH! Used the wrong frequency for the C band: we want 5.785 GHz. Regenerated antenna.
    [cpa-v4-5.765.brd, cpa-v4-5.785.brd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]
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2012-05-16 board tweaks for clearance, etc
    [gps-carrier.brd, gps-carrier.sch]
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2012-05-24 Moved board rev to bottom of board so we didn't get charged for two silk screens.
    [imu-adapter.brd]
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2012-08-15 Added blank battery board, used to laser cut out the back plate. Added latest "short" (4S1P) version of the battery sensor board. Added the battery breakout board, which adds a fuse to the battery. A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
    [battery-board-blank.brd, battery-board.brd, battery-board.sch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]
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2012-10-10 Added old NODE5 debugging cable, which uses the flex cable.
    [node5-debug-cable.brd, node5-debug-cable.sch]
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2013-02-10 Fixed error in dimensions and created device; may be missing layers in the package editor
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2013-03-04 Added labels in Battery Charger Page and fixed pad size in SIS412DN library
    [batterycharger_page.sch]
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2013-03-09 Brought ethernet up to e407 daughter board and connected via caps to rocketnet connector. Made cutout in board an internal cutout just for TH caps on e407 to gain stability in daugher board. Misc cle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
    [e407-sensor-shield.brd, e407-sensor-shield.sch]
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2013-03-16 Updated nets, removed headers on batterycharger, corrected BQ24725, BSS138W, SIS412 package outlines, added PG and FLT LED indicators and fixed nets on mcu_page
    [batterycharger_page.sch, mcu_page.sch]
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2013-03-25 swapped out battery charger schematic; modified symbols for BQ24725, BSS138W-7-F, FDS6680A, SiS412DN
    [batterycharger_page_isolated.sch]
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2013-03-27 updated library names; fixed ERC; flipped S and D of Q3 transistor
    [batterycharger_page_isolated.sch]
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2013-04-07 Swapped +18v layer with Route3 layer; changed layer names to Power, NS, EW
    [mcu_page.brd]
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2013-04-12 New rocketnet connector using bottom entry F 0.050" receptacle. Bolt placement and final upper-level PCB outline are probably not correct and are a TODO for when we prototype the connector.
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2013-04-23 Swapped out old connectors with the new male headers
    [mcu_page_combined.brd, mcu_page_combined.sch]
2013-04-23 Swapped out launch tower connector with the new male headers
    [mcu_page_combined.brd, mcu_page_combined.sch]
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2013-04-23 Moved connectors and rearranged status LEDs; fixed unconnected nets for Node 5
    [mcu_page_combined.brd, mcu_page_combined.sch]
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2013-05-02 Fixed overlapping TPs and GND ERC errors
    [mcu_page_combined.brd, mcu_page_combined.sch]
2013-05-02 Replaced Umbilical connector with 14-pin
    [mcu_page_combined.brd, mcu_page_combined.sch]
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2013-05-02 Added library parts: 1.27 mm 2x1 and 2x5 header; swapped out umbilical and debug connectors; added battery connector; added 2x1 header for BOOT0 to Vdd jumper
    [mcu_page_combined.brd, mcu_page_combined.sch]
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2013-05-04 Fixed some ERC issues; check Approved ERC for list of pending fixes
    [mcu_page_combined.brd, mcu_page_combined.sch]
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2013-05-05 Fixed DRC clearance issues
    [mcu_page_combined.brd]
2013-05-05 Replaced pull up resistors for ethernet switch
    [mcu_page_combined.brd]
2013-05-05 Fixed ground vias DRC errors
    [mcu_page_combined.brd]
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2013-05-09 Replaced capacitive coupling with new ALT4532 magnetics
    [mcu_page_combined.brd, mcu_page_combined.sch]
2013-05-09 Added missing center-tap resistor on the magnetics rocketnet connector side
    [mcu_page_combined.brd, mcu_page_combined.sch]
2013-05-09 Fixed ERC errors including missing connections (not actually connected to the same net)
    [mcu_page_combined.brd, mcu_page_combined.sch]
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2013-05-10 Swapped out rlc components with rlc_custom; added magnetics to umbilical connector; replaced 3v3 jumper with a 50 mil header; reorientated TX/RX status LEDs
    [mcu_page_combined.brd, mcu_page_combined.sch]
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2013-05-14 Fixed unconnected nodes on umbilical connector
    [mcu_page_combined.brd, mcu_page_combined.sch]
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2013-05-19 Added 18 pin umbilical with power and Ethernet broken out.
2013-05-19 Fixed symbol for 25 MHz 4-SMD capacitor
2013-05-19 Replaced 25 MHz crystal with 4-SMD crystal component
    [mcu_page_combined.brd, mcu_page_combined.sch]
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2013-05-19 Connected GND to GNDA; Replaced LTC with 18-pin header; Redid NodeX_Vout fill; Removed spare capacitor on magnetics
    [mcu_page_combined.brd, mcu_page_combined.sch]
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2013-05-21 Fixed/added erroneous component values, removed RST_N signal from the Ethernet reset, fixed naming/pinout on ICs/headers, added frames for each page
    [mcu_page_combined.brd, mcu_page_combined.sch]
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2013-05-23 replaced battery charger components to smallest avail, changed parts to nosilk
    [mcu_page_combined.sch]
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2013-05-23 Tidied schematics up; fixed PGOOD jumper
    [mcu_page_combined.brd, mcu_page_combined.sch]
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2013-05-24 Replaced passives with No-Silk outline; moved components on the board to approximate location
    [mcu_page_combined.brd, mcu_page_combined.sch]
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2013-05-27 Fixed DRC issues; cleaned up high-speed routing; cleaned up circuitry under KS8999 IC
    [mcu_page_combined.brd, mcu_page_combined.sch]
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2013-05-28 fixed auto router to route brd. 3 nets need manual connection, power fills, and DRC outstanding.
    [mcu_page_routed.job.brd]
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2013-05-29 Added stupid EAGLE temporary files to the gitignore. Updated IMU adapter with sane net names so we could easily trace nets. And updated the e407 shield to add a RGB LED, correct some schematic mistak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
    [e407-sensor-shield.brd, e407-sensor-shield.sch, imu-adapter-e407.brd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]
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2013-06-05 Fixed DRCs and approved stopmask warnings
    [mcu_page_combined_routed.brd]
2013-06-05 Fixed more DRCs; moved caps under STM32; added +3v3 fill
    [mcu_page_combined_routed.brd]
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2013-06-05 Started fixing autorouter nets
    [mcu_page_combined_routed.brd]
2013-06-05 Fixed missing airwires, added +3v3 fill on bottom board
    [mcu_page_combined_routed.brd]
2013-06-05 Added a 1x3 50mil header for I2C interface, added 10k pulldown on U15 pin N1, fixed +3v3 nets on bottom area of the board
    [mcu_page_combined_routed.brd, mcu_page_combined_routed.sch]
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2013-06-05 Fixed more routing
    [mcu_page_combined_routed.brd]
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2013-06-05 Updated missing pin on KS8999 and schematic
    [mcu_page_combined_routed.brd, mcu_page_combined_routed.sch]
2013-06-05 Removed changes made from previous commit--need to replace KS8999, not delete and add updated part
    [mcu_page_combined_routed.brd, mcu_page_combined_routed.sch]
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2013-06-07 fixed rout
    [mcu_page_combined_routed.brd]
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2013-06-08 fixed routing
    [mcu_page_combined_routed.brd]
2013-06-08 fixed all drc issues
    [mcu_page_combined_routed.brd]
2013-06-08 fixed thermal creation in poly's
    [mcu_page_combined_routed.brd]
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2013-06-09 finished layout, no airwires, no unapproved DRC errors, ready for silk
    [mcu_page_combined_routed.brd]
2013-06-09 Fixed routes
    [mcu_page_combined_routed.brd]
2013-06-09 Fixed more routes
    [mcu_page_combined_routed.brd]
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2013-06-09 Added more vias to LTM8023 layout area; fixed unconnected airwires
    [mcu_page_combined_routed.brd]
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2013-06-09 clean up on routing, added gnd fill to top and bottom, approved all DRC errors or fixed them.
    [mcu_page_combined_routed.brd]
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2013-06-10 Replaced 2 ohm resistor; updated bom
    [BOM_sc.xlsx, mcu_page_combined_routed.brd, mcu_page_combined_routed.sch]
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2013-06-10 Fixed name in silk screen layer
    [mcu_page_combined_routed.brd]
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2013-06-12 Various changes to daughterboards, including updating libraries, etc. ISSUE: Connectors still flipped on "bottom" of boards.
    [battery-board.brd, battery-board.sch, e407-roll-control.brd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]
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2013-06-12 Cleaned up layers 14, 15, and most of 16 although there are still some issues there.
    [mcu_page_combined_routed.brd]
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2013-06-15 Huge cleanup of power planes and vias. Removed secondary ground planes around KSZ, which was causing DRC errors.
    [mcu_page_combined_routed.brd, mcu_page_combined_routed.sch]
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2013-06-15 Cleanup around STM32 - JTAG, UART. Replaced small signal N and P channel MOSFETs with known parts.
    [mcu_page_combined_routed.brd, mcu_page_combined_routed.sch]
2013-06-15 Clean up of decoupling caps and feeds around STM32. Fixed mistake in VCAP1/VCAP2 capacitors.
    [mcu_page_combined_routed.brd, mcu_page_combined_routed.sch]
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2013-06-17 Replaced LEDs with all the same chipled. Cleaned up rocketnet connectors 4-8, only 1-3 left.
    [mcu_page_combined_routed.brd, mcu_page_combined_routed.sch]
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2013-06-17 Cleaned up rocketnet connectors 1-3. No DRC errors.
    [mcu_page_combined_routed.brd]
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2013-06-17 JJ found a subtle error: Layer 14's VIN plane had thermals, which would have cut down current capability. Fixed.
    [mcu_page_combined_routed.brd]
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2013-07-16 Checked and updated rocketnet hub BOM, adding DK part numbers. Also fixed some values in the EAGLE files to make the BOM collapse correctly. Added some voltage requirements on caps where necessary.
    [BOM_sc.xlsx, mcu_page_combined_routed.brd, mcu_page_combined_routed.sch]
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2014-01-08 Generated BOM and made a Digi-Key order. Found an ERC error that popped up, double checked part values in writeup.
    [battery-board-bom.xls, battery-board.brd, battery-board.sch]
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2014-01-09 OMG, did I really do that? Yes, apparently I did. Moved wire vias to the CORRECT side of the daughterboard.
    [rocketnet-daughter-16-RA.brd]
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2014-02-26 Fixed gearcam transistor (no 5V to the RP!!11!), made power wires bigger, fixed tname.
    [raspi-rnc.brd, raspi-rnc.sch]
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2014-03-15 Added proposed patches to the RNH, including for the NODE8 bug and for the new LED Ethernet link detect.
    [mcu_page_combined_routed.brd, mcu_page_combined_routed.sch]
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2014-05-28 wifi board outline to avoid bolts
    [wifi-carrier.brd]
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2014-06-21 Fixed unplated through #4 standoff.
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2014-06-25 Note to remove RG2 *and* F3. Fixed TP6 that was mirrored (weird) and and a tname collision. Otherwise, schematically the same as what was sent to OSHPark today.
    [raspi-rnc.brd]
2014-08-06 Fixed silk screen on umbilical cable - was wrong on RNC Umb v2 board!
    [rocketnet-daughter-18-RA-down.brd]
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

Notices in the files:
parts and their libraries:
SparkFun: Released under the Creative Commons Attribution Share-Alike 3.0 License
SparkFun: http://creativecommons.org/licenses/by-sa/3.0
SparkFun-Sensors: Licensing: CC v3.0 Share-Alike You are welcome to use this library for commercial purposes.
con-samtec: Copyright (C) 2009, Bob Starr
